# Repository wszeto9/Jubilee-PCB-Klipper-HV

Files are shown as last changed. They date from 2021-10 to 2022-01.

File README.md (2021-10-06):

# Jubilee-PCB-klipper
A high performance, high voltage custom PCB designed for the Jubilee 3D printer to run the Klipper firmware. 

<h2> Features:</h2>
<ul>
<li>5 Stepstick drivers(Up to 60V) with support for 2 additional external steppers</li>
<li>6 Heater outputs, capable of up to 60V or higher depending on chosen mosfets</li>
<li>12 DC fan outputs, each capable of 60V/2A</li>
<li>7 12V, 4-wire PWM fan outputs</li>
<li>5 thermistors</li>
<li>3 SPI buses</li>
<li>3 endstops</li>
<li>3 ADC inputs</li>
<li>3 5V servo outputs</li>
<li>BLtouch or microswitch Z endstop sensor</li>
<li>Neopixel ARGB header</li>
</ul>

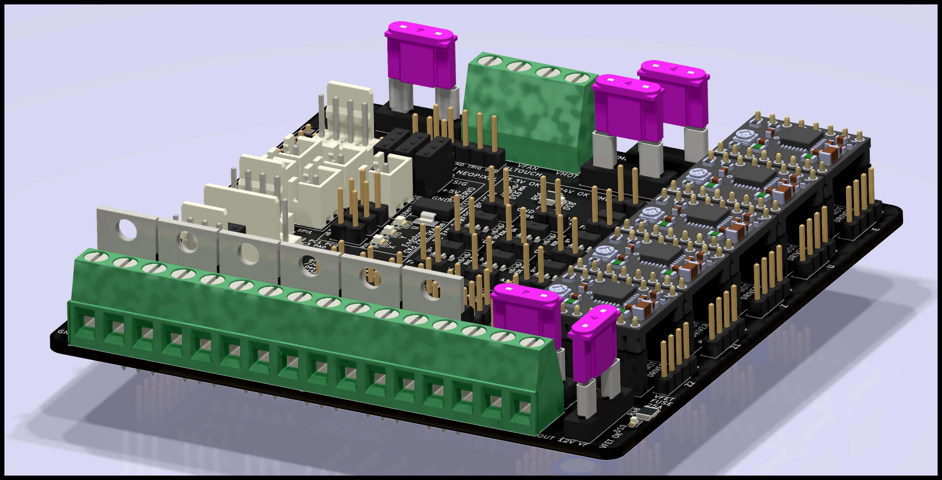
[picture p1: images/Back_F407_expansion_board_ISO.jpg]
ISO


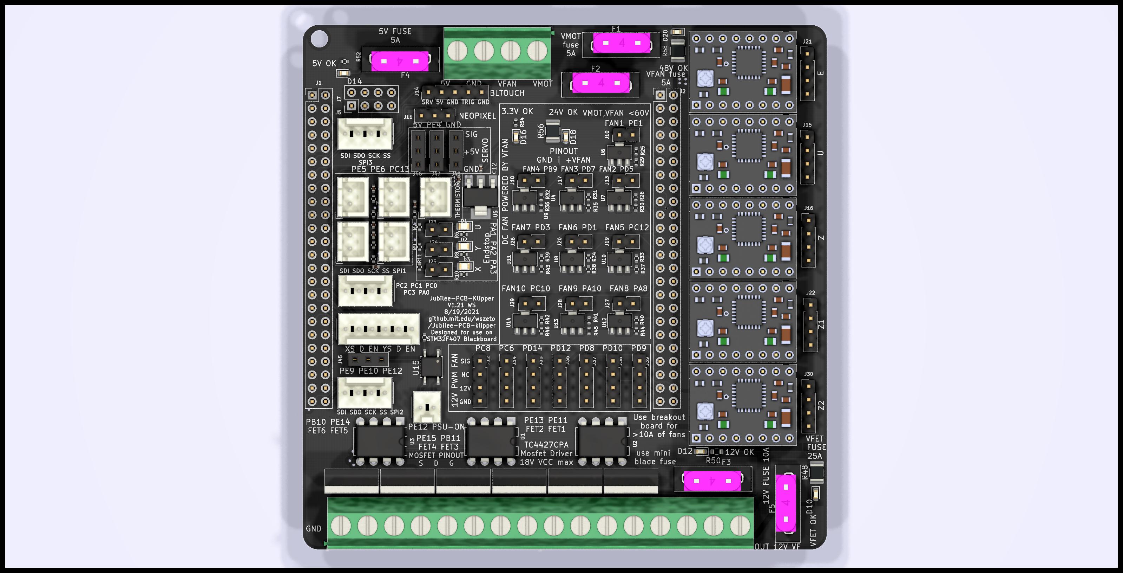
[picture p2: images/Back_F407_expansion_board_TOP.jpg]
TOP


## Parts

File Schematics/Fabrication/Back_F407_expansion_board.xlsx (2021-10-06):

Comment | Designator | Footprint | LCSC
2N7002 | Q7,Q8,Q17,Q18,Q23 | Package_TO_SOT_SMD:SOT-23 | C8545
4700R | R1,R5,R16,R18,R21 | Resistor_SMD:R_0402_1005Metric | C25900
10uF | C6,C7,C8,C9,C10,C11,C12 | Capacitor_SMD:C_0402_1005Metric | C15525
LED | D10,D12,D14,D16,D18,D20 | LED_SMD:LED_0603_1608Metric | C2290
LED | D1,D2,D3 | LED_SMD:LED_0805_2012Metric | C2293
10K | R3,R4,R6,R8,R10,R12,R13,R14,R15,R29,R30,R35,R36,R37,R38,R43,R44,R45,R46 | Resistor_SMD:R_0402_1005Metric | C25744
100R | R7,R9,R11 | Resistor_SMD:R_0402_1005Metric | C25076
300R | R25,R26,R31,R32,R33,R34,R39,R40,R41,R42 | Resistor_SMD:R_0402_1005Metric | C25102
7.5K | R47,R49,R51,R53,R55,R57 | Resistor_SMD:R_1210_3225Metric | C25890
1K | R50 | Resistor_SMD:R_0603_1608Metric | C21190
220 | R23,R52 | Resistor_SMD:R_0402_1005Metric | C25091
33 | R54 | Resistor_SMD:R_0402_1005Metric | C25105
AMS1117-3.3 | U5 | Package_TO_SOT_SMD:SOT-223-3_TabPin2 | C6186
EL357N(B)(TA)-G | U15 | Package_SO:SOP-4_3.8x4.1mm_P2.54mm | C6649

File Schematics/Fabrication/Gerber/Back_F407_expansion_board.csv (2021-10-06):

Comment | Designator | Footprint | LCSC
StepStick_Z | A1 | Module:Pololu_Breakout-16_15.2x20.3mm
StepStick_U | A2 | Module:Pololu_Breakout-16_15.2x20.3mm
StepStick_E | A3 | Module:Pololu_Breakout-16_15.2x20.3mm
StepStick_Z1 | A4 | Module:Pololu_Breakout-16_15.2x20.3mm
StepStick_Z2 | A5 | Module:Pololu_Breakout-16_15.2x20.3mm
63V/100uF | C1,C2,C3,C4,C5 | Capacitor_THT:CP_Radial_D8.0mm_P3.80mm
10uF | C6,C7,C8,C9,C10,C11,C12 | Capacitor_SMD:C_0402_1005Metric | C15525
LED | D10,D12,D14,D16,D18,D20 | LED_SMD:LED_0603_1608Metric | C2290
LED | D1,D2,D3 | LED_SMD:LED_0805_2012Metric | C2293
D_Schottky | D4,D5,D6,D7,D8 | Diode_SMD:D_SOD-123
LED | D9,D11,D13,D15,D17,D19 | LED_SMD:LED_1206_3216Metric
Fuse | F1,F2,F3,F4,F5 | Arduino:Fuseholder_Blade_Mini_aliexpress
Conn_02x24_MCULeft | J1 | Connector_PinHeader_2.54mm:PinHeader_2x24_P2.54mm_Vertical
Neopixel header | J11 | Connector_PinHeader_2.54mm:PinHeader_1x03_P2.54mm_Vertical
Conn_01x04_Male | J12,J34,J35,J36,J37,J38,J39 | Connector_PinHeader_2.54mm:PinHeader_1x04_P2.54mm_Vertical
Conn_01x02_Male | J10,J13,J17,J18,J19,J20,J26,J27,J28,J29 | Connector_PinHeader_2.54mm:PinHeader_1x02_P2.54mm_Vertical
BLTouch | J14 | Connector_PinHeader_2.54mm:PinHeader_1x05_P2.54mm_Vertical
U | J15 | Connector_PinHeader_2.54mm:PinHeader_1x04_P2.54mm_Vertical
Z | J16 | Connector_PinHeader_2.54mm:PinHeader_1x04_P2.54mm_Vertical
Conn_02x24_MCURight | J2 | Connector_PinHeader_2.54mm:PinHeader_2x24_P2.54mm_Vertical
E | J21 | Connector_PinHeader_2.54mm:PinHeader_1x04_P2.54mm_Vertical
Z1 | J22 | Connector_PinHeader_2.54mm:PinHeader_1x04_P2.54mm_Vertical
U_LIM | J23 | Connector_PinHeader_2.54mm:PinHeader_1x02_P2.54mm_Vertical
Y_LIM | J24 | Connector_PinHeader_2.54mm:PinHeader_1x02_P2.54mm_Vertical
X_LIM | J25 | Connector_PinHeader_2.54mm:PinHeader_1x02_P2.54mm_Vertical
XYStepDirEn | J3 | Connector_Molex:Molex_KK-254_AE-6410-06A_1x06_P2.54mm_Vertical
Z2 | J30 | Connector_PinHeader_2.54mm:PinHeader_1x04_P2.54mm_Vertical
Screw_Terminal_01x04 | J31 | TerminalBlock_Phoenix:TerminalBlock_Phoenix_MKDS-1,5-4-5.08_1x04_P5.08mm_Horizontal
Screw_Terminal_01x08 | J32,J33 | TerminalBlock_Phoenix:TerminalBlock_Phoenix_MKDS-1,5-8-5.08_1x08_P5.08mm_Horizontal
spi1 | J4 | Connector_Molex:Molex_KK-254_AE-6410-04A_1x04_P2.54mm_Vertical
Conn_02x03_Odd_Even | J40,J41,J42,J43,J44 | Connector_PinHeader_2.54mm:PinHeader_2x03_P2.54mm_Vertical
Conn_01x03_Female | J45,J46,J47,J48 | Connector_PinSocket_2.54mm:PinSocket_1x03_P2.54mm_Vertical
spi3 | J5 | Connector_Molex:Molex_KK-254_AE-6410-04A_1x04_P2.54mm_Vertical
spi2 | J6 | Connector_Molex:Molex_KK-254_AE-6410-04A_1x04_P2.54mm_Vertical
NRF24L01 | J7 | Connector_PinHeader_2.54mm:PinHeader_2x04_P2.54mm_Vertical
Conn_01x02_Male | J8 | Connector_Molex:Molex_KK-254_AE-6410-02A_1x02_P2.54mm_Vertical
IRFB7545PBF | Q1,Q2,Q3,Q4,Q5,Q6 | Package_TO_SOT_THT:TO-220-3_Vertical
2N7002 | Q7,Q8,Q17,Q18,Q23 | Package_TO_SOT_SMD:SOT-23 | C8545
4700R | R1,R5,R16,R18,R21 | Resistor_SMD:R_0402_1005Metric | C25900
Thermistor 2 | R17 | Connector_JST:JST_XH_B2B-XH-A_1x02_P2.50mm_Vertical
Thermistor 1 | R19 | Connector_JST:JST_XH_B2B-XH-A_1x02_P2.50mm_Vertical
Thermistor 5 | R2 | Connector_JST:JST_XH_B2B-XH-A_1x02_P2.50mm_Vertical
Thermistor 4 | R20 | Connector_JST:JST_XH_B2B-XH-A_1x02_P2.50mm_Vertical
Thermistor 3 | R22 | Connector_JST:JST_XH_B2B-XH-A_1x02_P2.50mm_Vertical
300R | R25,R26,R31,R32,R33,R34,R39,R40,R41,R42 | Resistor_SMD:R_0402_1005Metric | C25102
7.5K | R47,R49,R51,R53,R55,R57 | Resistor_SMD:R_1210_3225Metric | C25890
1K | R50 | Resistor_SMD:R_0603_1608Metric | C21190
220 | R23,R52 | Resistor_SMD:R_0402_1005Metric | C25091
33 | R54 | Resistor_SMD:R_0402_1005Metric | C25105
7.5K | R48,R56,R58 | Resistor_SMD:R_1210_3225Metric_Pad1.30x2.65mm_HandSolder
10K | R3,R4,R6,R8,R10,R12,R13,R14,R15,R29,R30,R35,R36,R37,R38,R43,R44,R45,R46 | Resistor_SMD:R_0402_1005Metric | C25744
100R | R7,R9,R11 | Resistor_SMD:R_0402_1005Metric | C25076
4427 FET driver 2 | U1 | Package_DIP:DIP-8_W7.62mm
EL357N(B)(TA)-G | U15 | Package_SO:SOP-4_3.8x4.1mm_P2.54mm | C6649
4427 FET driver 1 | U2 | Package_DIP:DIP-8_W7.62mm
4427 FET driver 3 | U3 | Package_DIP:DIP-8_W7.62mm
BSS87 | U4,U6,U7,U8,U9,U10,U11,U12,U13,U14 | Package_TO_SOT_SMD:SOT-89-3 | C879078
AMS1117-3.3 | U5 | Package_TO_SOT_SMD:SOT-223-3_TabPin2 | C6186

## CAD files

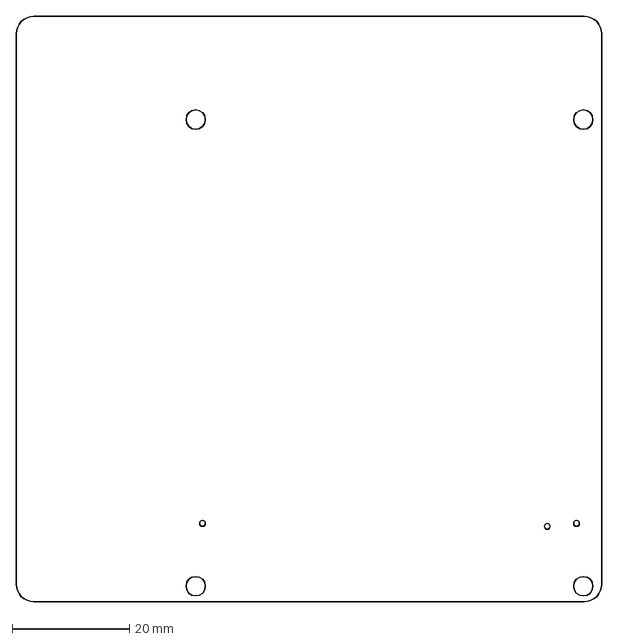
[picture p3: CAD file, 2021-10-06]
Schematics/cutout_outline.dxf
100.0 x 100.0 mm

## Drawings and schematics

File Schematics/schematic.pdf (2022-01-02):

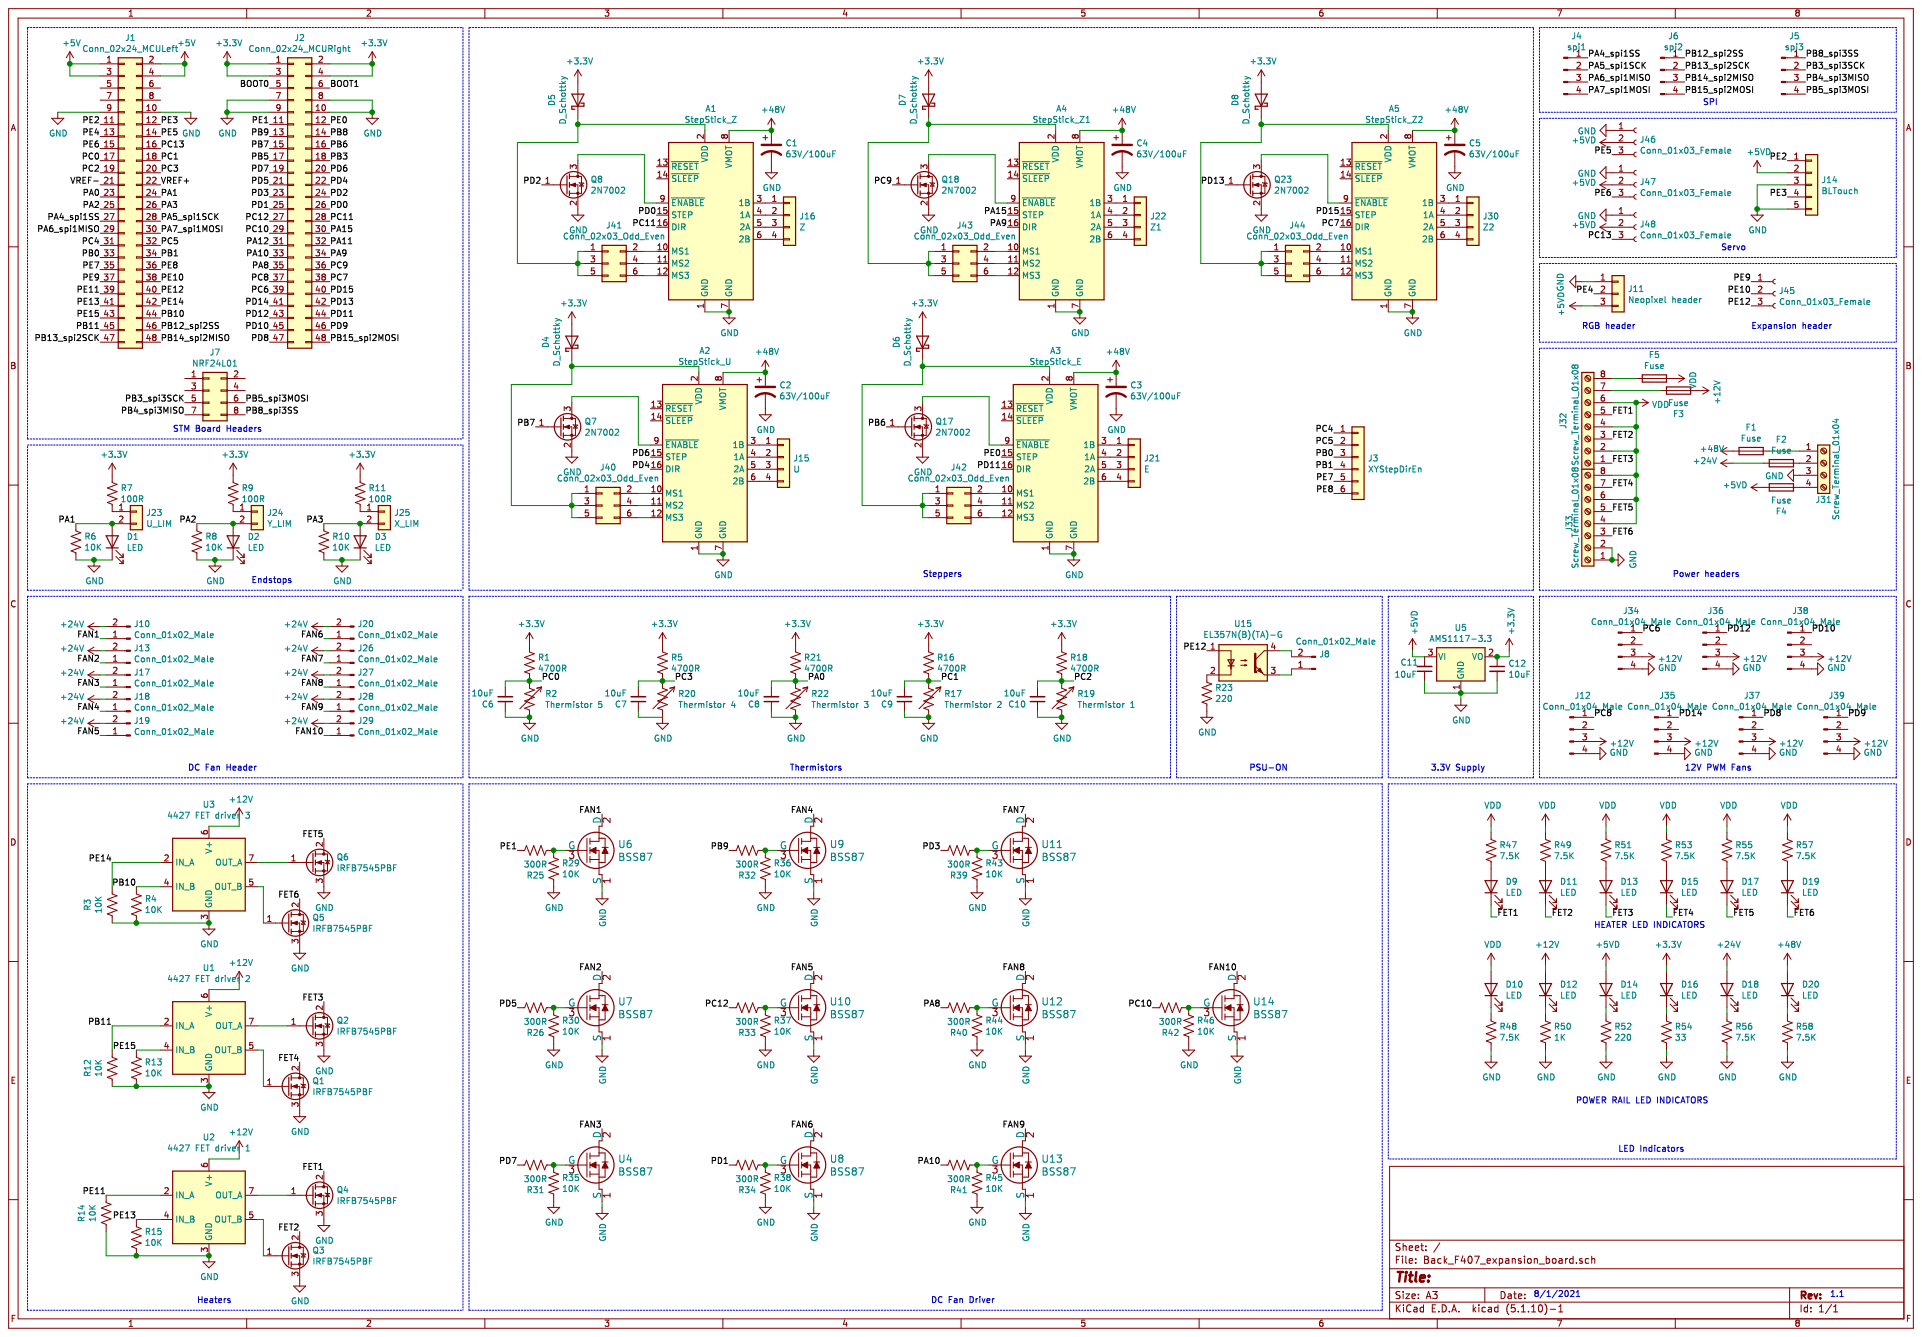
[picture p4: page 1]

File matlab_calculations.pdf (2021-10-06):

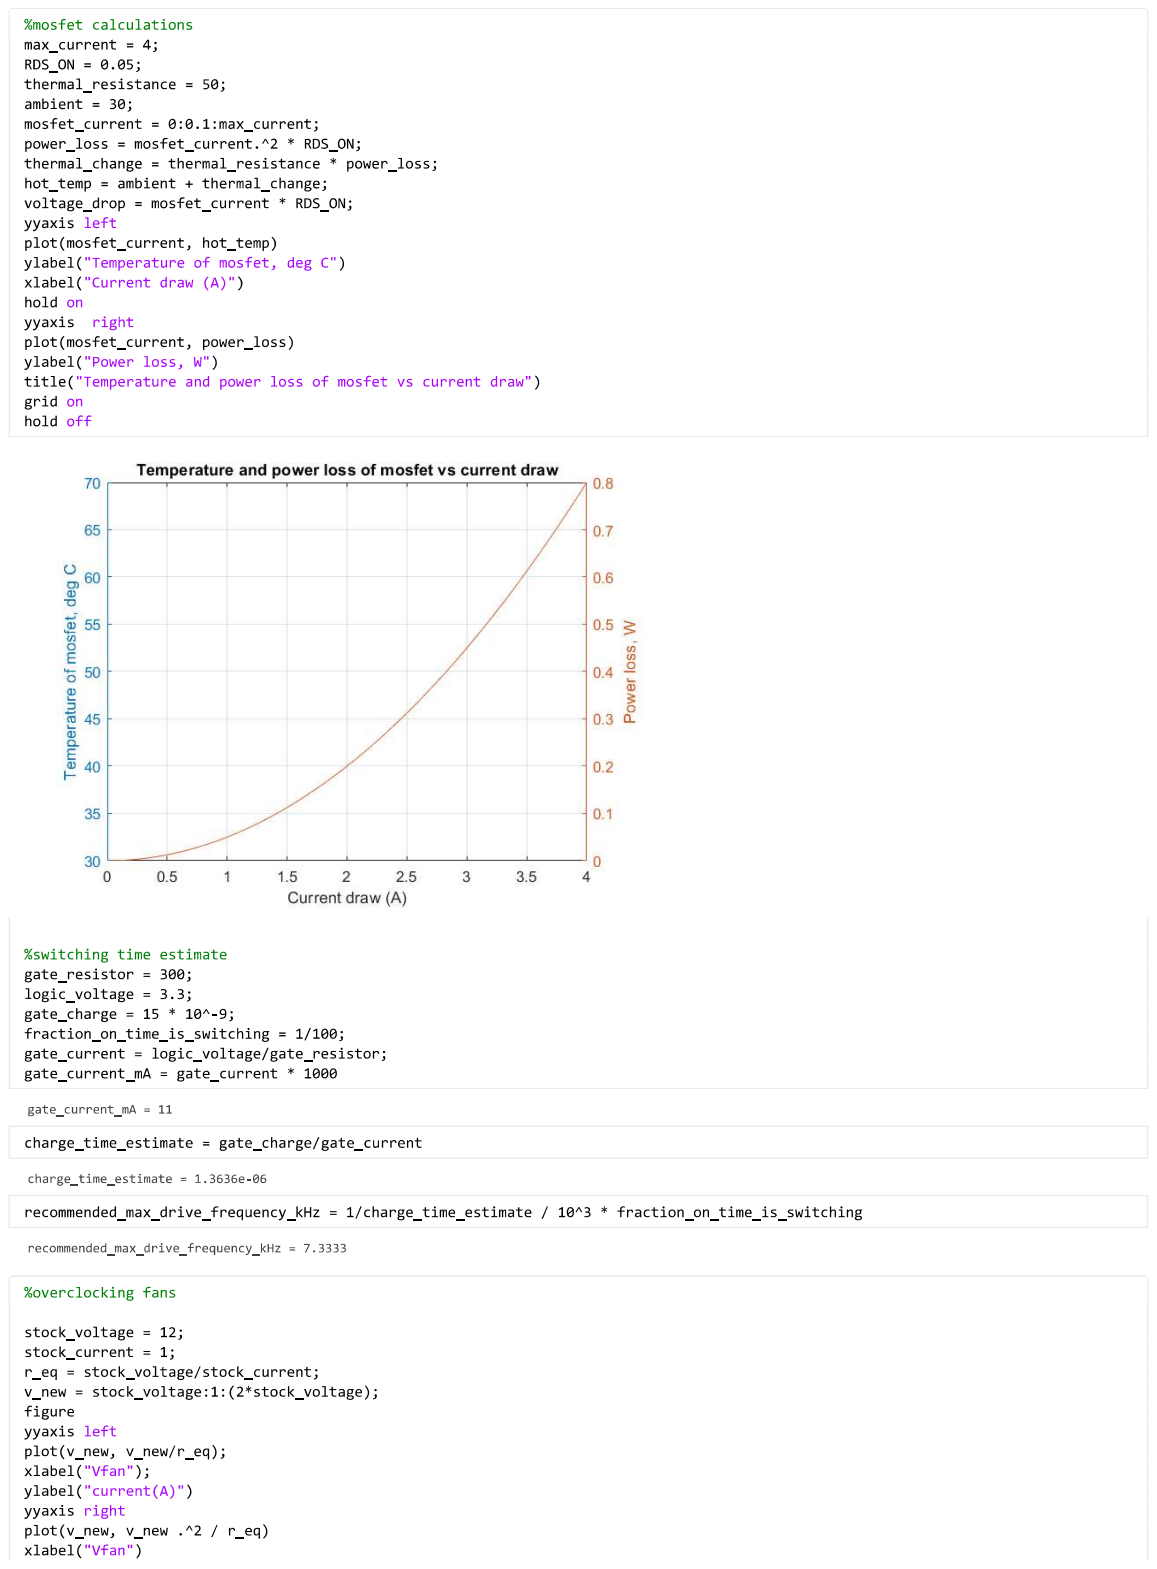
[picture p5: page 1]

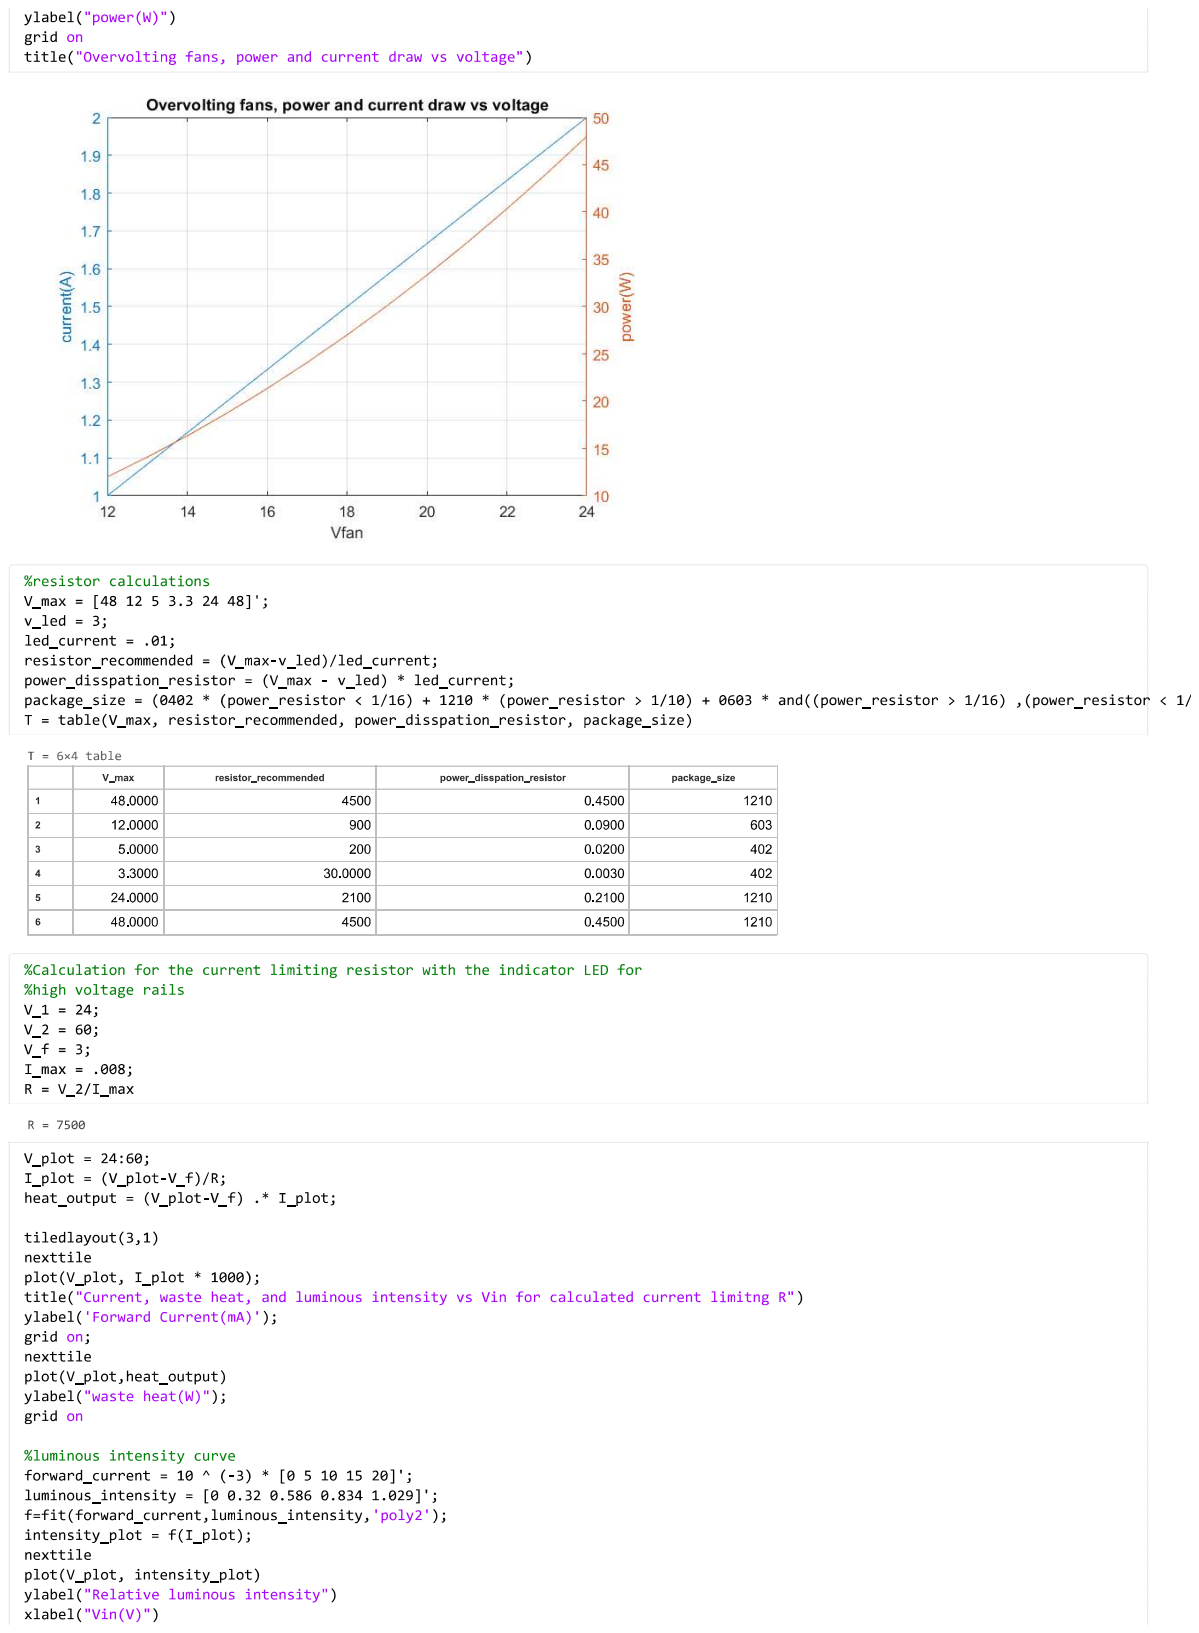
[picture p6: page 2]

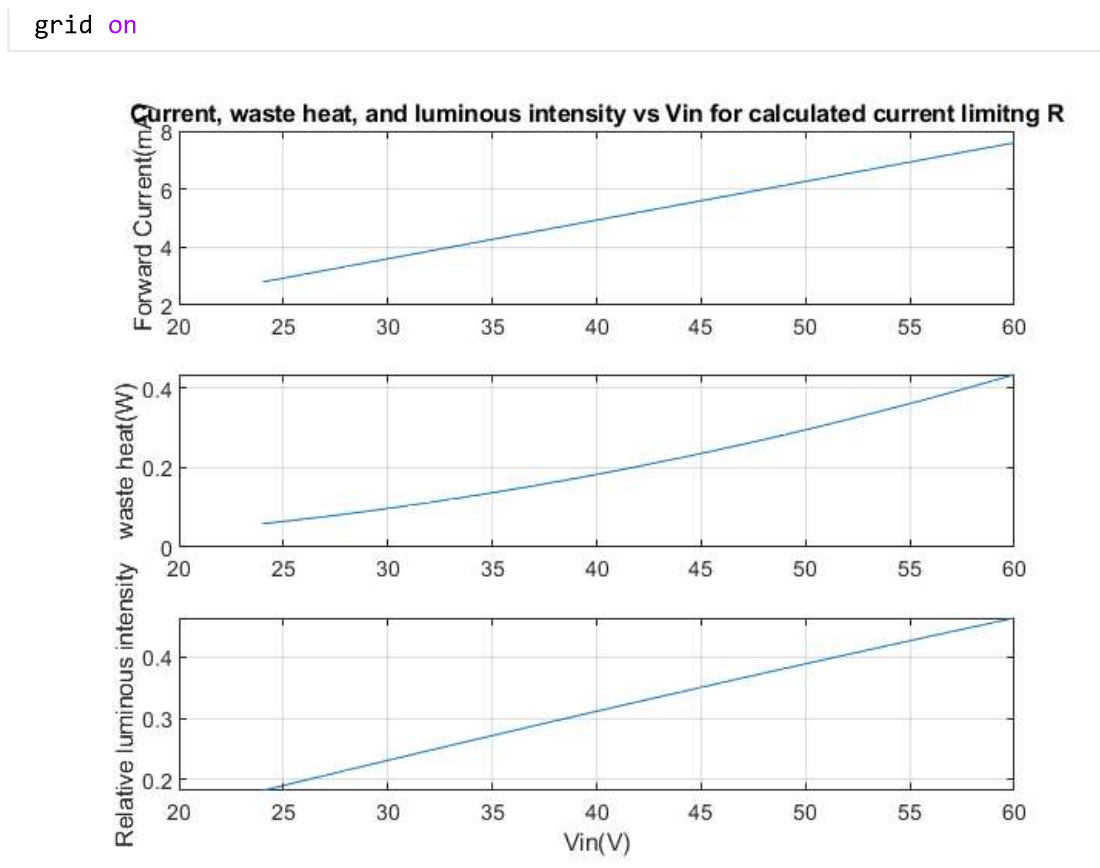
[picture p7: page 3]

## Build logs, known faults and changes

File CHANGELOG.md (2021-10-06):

V1.2
-PB3 reserved for SPI3
-PB5 ^
-Stepper U remapped to PB7 EN PD6 STEP PD4 DIR
-BLtouch 5V and SIG switched
-silkscreen for motor driver changed
-mosfets changed for one with a lower RDS on at 3V VGS

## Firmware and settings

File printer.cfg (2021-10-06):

[mcu host]
serial: /tmp/klipper_host_mcu

[mcu]
#serial:/dev/ttyACM0
restart_method:rpi_usb
serial: /dev/serial/by-path/platform-3f980000.usb-usb-0:1.4:1.0

[temperature_sensor raspberry_pi]
sensor_type: temperature_host
min_temp: 10
max_temp: 100

[temperature_sensor mcu_temp]
sensor_type: temperature_mcu
min_temp: 0
max_temp: 100

[virtual_sdcard]
path: ~/gcode_files

[pause_resume]
[display_status]

[neopixel lights]
pin: PE4
chain_count:15
color_order: GRB

[adxl345]
cs_pin: PB12
spi_bus: spi2

[resonance_tester]
accel_chip: adxl345
probe_points:
    150,150,20  # an example

[stepper_x]
step_pin: PC4
dir_pin: PC5
enable_pin: PB0
rotation_distance: 40
full_steps_per_rotation: 200
endstop_pin: !PA1
position_endstop: -11.5
position_max: 311.5
position_min: -11.5
homing_speed: 200
second_homing_speed:30
microsteps: 16

[tmc2130 stepper_x]
cs_pin: PB8
spi_bus:spi3
run_current: 2
hold_current: 0.75
sense_resistor: 0.022

[stepper_y]
step_pin: PB1
dir_pin: PE7
enable_pin: PE8
rotation_distance: 40
full_steps_per_rotation: 200
endstop_pin: !PA2
position_endstop: -44.0
position_max: 345
position_min: -44.0
homing_speed: 200
second_homing_speed:30
microsteps: 16

[tmc2130 stepper_y]
cs_pin: PA4
spi_bus:spi1
run_current: 2
hold_current:0.75
sense_resistor: 0.022

[manual_stepper tool_lock]
step_pin: PB3
dir_pin: PD6
enable_pin: PD4
microsteps: 32
rotation_distance: 360
full_steps_per_rotation: 200
gear_ratio: 3:1
endstop_pin: !PA3
velocity:100


[stepper_z]
step_pin: PD0
dir_pin: !PC11
enable_pin: PD2
rotation_distance: 2
full_steps_per_rotation: 200
microsteps:16
endstop_pin: probe:z_virtual_endstop
position_max: 330
position_min: -5
homing_speed: 50

[stepper_z1]
step_pin: PA15
dir_pin: !PC9
enable_pin: PA9
rotation_distance: 2
full_steps_per_rotation: 200
microsteps:16

[stepper_z2]
step_pin: PC7
dir_pin: !PD13
enable_pin: PD15
rotation_distance: 2
full_steps_per_rotation: 200
microsteps:16

[bltouch]
sensor_pin: ^PE2
control_pin: PE3
z_offset: 2.01

[safe_z_home]
home_xy_position: 150,10
speed: 50
z_hop: 15
z_hop_speed: 5

[bed_mesh]
mesh_min: 30,30
mesh_max: 270,270
probe_count: 5,5
speed: 300

[z_tilt]
z_positions:
	150, -16.5
	297.5,313.5
	2.5,313.5
points:
	150,10
	290,290
	10,290
speed:300

[force_move]
enable_force_move: true

[extruder]
step_pin: PE0
dir_pin: PD11
enable_pin: PB6
heater_pin:PE15
sensor_pin: PC0
step_distance: .00225
nozzle_diameter: 0.400
filament_diameter: 1.750
sensor_type: EPCOS 100K B57560G104F
control: pid
pid_Kp: 22.2
pid_Ki: 1.08
pid_Kd: 114
min_temp: 0
max_temp: 290

[thermistor NTCALUG01A103F]
temperature1: 25.
resistance1: 10000.
beta: 3984

[heater_fan DCfan1]
pin: PE1
heater: extruder

[fan_generic DCfan2]
pin:PB9

[fan_generic DCfan3]
pin:PB7

[fan_generic DCfan4]
pin:PB5

[fan_generic DCfan5]
pin:PD7

[fan_generic DCfan6]
pin:PD5

[fan_generic DCfan7]
pin:PD3

[fan_generic DCfan8]
pin:PD1

[fan_generic DCfan9]
pin:PC12

[fan_generic DCfan10]
pin:PC10

[fan_generic DCfan11]
pin:PA10

[fan_generic DCfan12]
pin:PA8

[output_pin pwmfan1]
pin: PC8
pwm:true
cycle_time: 0.00004
value:0

[output_pin pwmfan2]
pin: PC6
pwm:true
cycle_time: 0.00004
value:0

[output_pin pwmfan3]
pin: PD14
pwm:true
cycle_time: 0.00004
value:0

[output_pin pwmfan4]
pin: PD12
pwm:true
cycle_time: 0.00004
value:0

[output_pin pwmfan5]
pin: PD10
pwm:true
cycle_time: 0.00004
value:0

[output_pin pwmfan6]
pin: PD8
pwm:true
cycle_time: 0.00004
value:0

[output_pin pwmfan7]
pin: PD9
pwm:true
cycle_time: 0.00004
value:0

[heater_bed]
heater_pin: PB11
sensor_pin: PC1 # T0
sensor_type: NTC 100K MGB18-104F39050L32
control: pid
pid_Kp: 62.491
pid_Ki: 1.009
pid_Kd: 967.831
min_temp: 0
max_temp: 130

#Since klipper currently doesn't have proper support for M106/M107
#we need to add a PWM output and write some gcode macros to fix it
#[output_pin tool2_fan]
#pin: PE15
#pwm:true
#cycle_time: 0.00004
#value:0

[printer]
kinematics: corexy
max_velocity: 1000
max_accel: 400000
max_z_velocity: 5
max_z_accel: 100
square_corner_velocity: 25.0

[input_shaper]
shaper_freq_x: 98.6
shaper_type_x: zv
shaper_freq_y: 52.4
shaper_type_y: mzv

[gcode_macro CANCEL_PRINT]
rename_existing: BASE_CANCEL_PRINT
gcode:
  TURN_OFF_HEATERS
  CLEAR_PAUSE
  SDCARD_RESET_FILE
  BASE_CANCEL_PRINT

[gcode_macro RESET_TMC]
gcode:
  INIT_TMC STEPPER=stepper_x
  SET_TMC_FIELD STEPPER=stepper_x FIELD=reset VALUE=1
  SET_TMC_FIELD STEPPER=stepper_x FIELD=uv_cp VALUE=1
  INIT_TMC STEPPER=stepper_y
  SET_TMC_FIELD STEPPER=stepper_y FIELD=reset VALUE=1
  SET_TMC_FIELD STEPPER=stepper_y FIELD=uv_cp VALUE=1

[gcode_macro TROUBLESHOOT_SET_HOME]
gcode:
    G0 X0 Y0 F10000
    SET_KINEMATIC_POSITION X=0 Y=0 Z=0

[gcode_macro INIT]
gcode:
    {% if not printer["gcode_macro DOCK_INIT"].tool_present %}
        g28
        Z_TILT_ADJUST
        g1 X10 Y10 F3000
        LOCK_INIT
		DOCK_INIT
    {% else %}
        { action_respond_info("You cannot run INIT with a tool in place, please run TOOL_UNLOCK and manually place the tool in its dock.") }
    {% endif %}

[gcode_macro DUMP_VARS]
gcode:
   {% for name1 in printer %}
      {% for name2 in printer[name1] %}
         { action_respond_info("printer['%s'].%s = %s" % (name1, name2, printer[name1][name2])) }
      {% endfor %}
   {% endfor %}

[gcode_macro T0]
gcode:
	TOOL_PICKUP ZONE_X=5 ZONE_Y=260 PARK_X=5 PARK_Y=341 OFFSET_X=4.5 OFFSET_Y=-44.02 OFFSET_Z=2.65
	ACTIVATE_EXTRUDER EXTRUDER=extruder

[gcode_macro T1]
gcode:
	TOOL_PICKUP ZONE_X=105 ZONE_Y=260 PARK_X=105 PARK_Y=341 OFFSET_X=4.5 OFFSET_Y=-44.67 OFFSET_Z=2.87
	ACTIVATE_EXTRUDER EXTRUDER=extruder1

[gcode_macro G28]
rename_existing:    G28.1
gcode:
    {%set p=[] %}    
    {% for key in params %}
        {% if key != 'G' %}
            {% set p = p.append(key + params[key])  %}
        {% endif %}
    {% endfor %}
	{% if not printer["gcode_macro DOCK_INIT"].tool_present%}
		G28.1 { p|join(" ") }
	{% else %}
	{ action_respond_info("You attemped to home while a tool is present") }
	{% endif %}

[idle_timeout]
gcode:
	{ action_respond_info( "Idle Timeout Reached!") }
	TURN_OFF_HEATERS
    M107 P0
    M107 P1
    {% if 'xyz' in printer.toolhead.homed_axes %}
        #Drop the Z 5mm relative
        G91;
        G1 Z5;
        #Set use back to absolute mode.
        G90;
        {% if printer["gcode_macro DOCK_INIT"].tool_present %}
                #If we have a tool, drop it off
                TOOL_DROPOFF
        {% elif printer["gcode_macro LOCK_INIT"].lock_state %}
                #If we don't have a tool but the lock is engaged, unlock it.
                TOOL_UNLOCK
        {% endif %}
    {% endif %}
	M84
timeout: 600

#*# <---------------------- SAVE_CONFIG ---------------------->
#*# DO NOT EDIT THIS BLOCK OR BELOW. The contents are auto-generated.
#*#
#*# [heater_bed]
#*#
#*# [bed_mesh default]
#*# version = 1
#*# points =
#*# 	  0.132492, 0.191242, 0.320617, 0.464367
#*# 	  -0.058758, -0.085633, -0.012508, 0.147492
#*# 	  -0.258133, -0.313133, -0.235633, -0.138758
#*# 	  -0.346883, -0.390633, -0.349383, -0.280008
#*# x_count = 4
#*# y_count = 4
#*# mesh_x_pps = 2
#*# mesh_y_pps = 2
#*# algo = lagrange
#*# tension = 0.2
#*# min_x = 10.0
#*# max_x = 289.99
#*# min_y = 10.0
#*# max_y = 289.99

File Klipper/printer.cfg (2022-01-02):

[mcu host]
serial: /tmp/klipper_host_mcu

[mcu]
serial: /dev/serial/by-id/usb-Klipper_stm32f407xx_1B0028001351383435353637-if00

[mcu front]
serial: /dev/serial/by-id/usb-Klipper_stm32f407xx_1D0028000247373033303731-if00

[temperature_sensor raspberry_pi]
sensor_type: temperature_host
min_temp: 10
max_temp: 100

[temperature_sensor mcu_back_temp]
sensor_type: temperature_mcu
min_temp: 0
max_temp: 100

[temperature_sensor mcu_front_temp]
sensor_type: temperature_mcu
sensor_mcu: front
min_temp: 0
max_temp: 100

[virtual_sdcard]
path: ~/gcode_files

[pause_resume]
[display_status]
[include MACROS.cfg]

[neopixel lights]
pin: PE4
chain_count:15
color_order: GRB

[adxl345]
cs_pin: PB8
spi_bus: spi3

[resonance_tester]
accel_chip: adxl345
probe_points:
    150,150,20

[input_shaper]
shaper_freq_x: 71.6
shaper_type_x: 2hump_ei
shaper_freq_y: 41
shaper_type_y: mzv

[stepper_x]
step_pin: PB1
dir_pin: PE7
enable_pin: PE8
rotation_distance: 40
full_steps_per_rotation: 200
endstop_pin: !PA3
position_endstop: -11.5
position_max: 311.5
position_min: -11.5
homing_speed: 200
second_homing_speed:30
microsteps: 16

[tmc2130 stepper_x]
cs_pin: PB12
spi_bus:spi2
run_current: 2
hold_current: 0.75
sense_resistor: 0.022

[stepper_y]
step_pin: PC4
dir_pin: PC5
enable_pin: PB0
rotation_distance: 40
full_steps_per_rotation: 200
endstop_pin: !PA2
position_endstop: -44.0
position_max: 345
position_min: -44.0
homing_speed: 200
second_homing_speed:30
microsteps: 16

[tmc2130 stepper_y]
cs_pin: PA4
spi_bus:spi1
run_current: 2
hold_current:0.75
sense_resistor: 0.022

[manual_stepper tool_lock]
step_pin: PE12
dir_pin: !PD6
enable_pin: PD4
microsteps: 32
rotation_distance: 360
full_steps_per_rotation: 200
gear_ratio: 3:1
endstop_pin: !PA1
velocity:100

[stepper_z]
step_pin: PD0
dir_pin: !PC11
enable_pin: PD2
rotation_distance: 2
full_steps_per_rotation: 200
microsteps:16
endstop_pin: probe:z_virtual_endstop
position_max: 330
position_min: -5
homing_speed: 50

[stepper_z1]
step_pin: PA15
dir_pin: !PA9
enable_pin: PC9
rotation_distance: 2
full_steps_per_rotation: 200
microsteps:16

[stepper_z2]
step_pin: !PD13
dir_pin: !PC7
enable_pin: PD15
rotation_distance: 2
full_steps_per_rotation: 200
microsteps:16

[bltouch]
sensor_pin: ^PE3
control_pin: PE2
#z_offset: 1.450
pin_move_time: 0.30

[safe_z_home]
home_xy_position: 150,10
speed: 50
z_hop: 15
z_hop_speed: 5

[bed_mesh]
mesh_min: 30,30
mesh_max: 270,270
probe_count: 5,5
speed: 300

[z_tilt]
z_positions:
	150, -16.5
	297.5,313.5
	2.5,313.5
points:
	150,10
	290,290
	10,290
speed:300

[force_move]
enable_force_move: true

[extruder]
step_pin: front:PE0
dir_pin: front:!PD11
enable_pin: front:PB6
heater_pin:front:PE11
sensor_pin: front:PC2
pullup_resistor: 4700
nozzle_diameter: 0.400
filament_diameter: 1.750
sensor_type: Generic 3950
pressure_advance: 0.0
#control: pid
#pid_Kp: 22.2
#pid_Ki: 1.08
#pid_Kd: 114
min_temp: 0
max_temp: 300
rotation_distance: 22.67895 #for 5mm Shaft Driven Bondtech gearsets
#gear_ratio: 50:10 #for standard 10t motor
gear_ratio: 50:8 #for sherpa mini 8t motor
microsteps: 16
full_steps_per_rotation: 200 #1.8deg Motor

max_extrude_only_distance: 1400.0
max_extrude_only_velocity: 75.0
max_extrude_only_accel: 4500

[firmware_retraction]
retract_length: 1
#   The length of filament (in mm) to retract when G10 is activated,
#   and to unretract when G11 is activated (but see
#   unretract_extra_length below). The default is 0 mm.
retract_speed: 30
#   The speed of retraction, in mm/s. The default is 20 mm/s.
#unretract_extra_length: 0
#   The length (in mm) of *additional* filament to add when
#   unretracting.
#unretract_speed: 10
#   The speed of unretraction, in mm/s. The default is 10 mm/s.

[thermistor NTCALUG01A103F]
temperature1: 25.
resistance1: 10000.
beta: 3984

[heater_fan H1FAN]
pin: front:PD5
heater: extruder

[heater_bed]
heater_pin: PE11
sensor_pin: PC1 # T0
pullup_resistor: 470
sensor_type: Generic 3950
#control: pid
#pid_Kp: 62.491
#pid_Ki: 1.009
#pid_Kd: 967.831
min_temp: 0
max_temp: 130

[printer]
kinematics: corexy
max_velocity: 1000
max_accel: 200000
max_z_velocity: 5
max_z_accel: 100
square_corner_velocity: 250.0

[gcode_macro RESET_TMC]
gcode:
  INIT_TMC STEPPER=stepper_x
  SET_TMC_FIELD STEPPER=stepper_x FIELD=reset VALUE=1
  SET_TMC_FIELD STEPPER=stepper_x FIELD=uv_cp VALUE=1
  INIT_TMC STEPPER=stepper_y
  SET_TMC_FIELD STEPPER=stepper_y FIELD=reset VALUE=1
  SET_TMC_FIELD STEPPER=stepper_y FIELD=uv_cp VALUE=1

[gcode_macro TROUBLESHOOT_SET_HOME]
gcode:
    G0 X0 Y0 F10000
    SET_KINEMATIC_POSITION X=0 Y=0 Z=0

[idle_timeout]
gcode:
	{ action_respond_info( "Idle Timeout Reached!") }
	TURN_OFF_HEATERS
    M107 P0
    M107 P1
	M84
timeout: 600

#*# <---------------------- SAVE_CONFIG ---------------------->
#*# DO NOT EDIT THIS BLOCK OR BELOW. The contents are auto-generated.
#*#
#*# [heater_bed]
#*# control = pid
#*# pid_kp = 44.440
#*# pid_ki = 3.613
#*# pid_kd = 136.654
#*#
#*# [bed_mesh default]
#*# version = 1
#*# points =
#*# 	0.117456, -0.059419, -0.011919, -0.142544, -0.196919
#*# 	0.075581, -0.027544, -0.086919, -0.113169, -0.201919
#*# 	0.044956, -0.018169, -0.093794, -0.095044, -0.188794
#*# 	-0.019419, -0.095669, -0.058169, -0.070669, -0.116919
#*# 	0.029956, -0.000044, -0.055044, -0.010044, -0.052544
#*# x_count = 5
#*# y_count = 5
#*# mesh_x_pps = 2
#*# mesh_y_pps = 2
#*# algo = lagrange
#*# tension = 0.2
#*# min_x = 30.0
#*# max_x = 270.0
#*# min_y = 30.0
#*# max_y = 270.0
#*#
#*# [extruder]
#*# control = pid
#*# pid_kp = 17.773
#*# pid_ki = 0.745
#*# pid_kd = 105.973
#*#
#*# [bltouch]
#*# z_offset = 1.900

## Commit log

2021-10-06 cloned from internal MIT github
    [Back_F407_expansion_board-B_Cu.gbr, Back_F407_expansion_board-B_Mask.gbr, Back_F407_expansion_board-B_Paste.gbr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]
2022-01-02 added config file
    [printer.cfg]
2022-01-02 updated schematic
